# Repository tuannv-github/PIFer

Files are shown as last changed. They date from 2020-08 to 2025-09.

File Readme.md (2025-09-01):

# PIFWRobot

<p align="center">
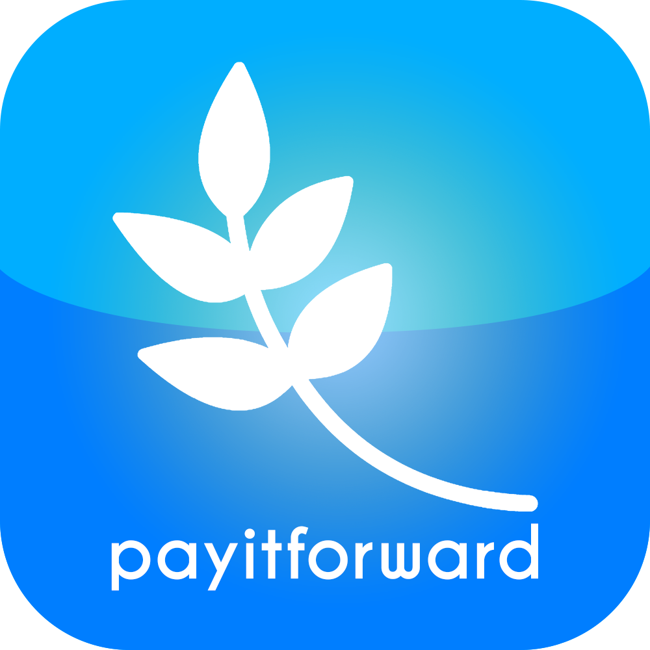
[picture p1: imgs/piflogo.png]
PIF Logo
  
</p>

PIFWRobot is an open source project for a two-wheeled self-balancing robot.

## Demo

Youtube:
* https://www.youtube.com/watch?v=qJoEQ5KJzxM&t=71s&pp=ygUjdHdvIHdoZWVsIHNlbGYgYmFsYW5jaW5nIHJvYm90IHR1YW4%3D
* https://www.youtube.com/watch?v=bJMFOIG7K60&t=61s

Without any velocity command, the robot is trying to stabilize itself. 
<p align="center">
  PIF Logo
</p>

## Repository Contents
* **firmware**: 
  * **balancing-robot**: The entire firmware for STM32F103C8T6 MCU
  * **esp8266_arduino**: ESP8266 Arduino based TCP server firmware
* **software**:
  * **GCSQt**: A Qt-based ground control station for remote controlling, calibration, and PID tuning
  * **mavlink**: Mavlink message definitions and code generation tools
* **hardware**:
  * **board**: Altium-designed schematic and PCB source for the main board
  * **frame**: SolidWorks-based frame source for the robot

## Hardware
*  1 STM32F103C8T6
*  1 MPU6050/9250
*  2 DC Motors with Encoder
*  1 ESP8266 for remote control, calibration, and PID tuning
*  1 L298 DC Motor Driver
*  1 12V Li-po battery 

## PID algorithm
Cascade PID:
* Inner loop: tilt controller
  * Input: 
    * Tilt set point from outer loop
    * Feed back tilt from sensor (MPU6050/9250)
  * Output:
    * PWM duty cycle for both motors
* Outer loop: velocity controller
  * Input:
    * Velocity command from rthe emote controller
    * Feed back velocity from encoder
  * Output:
    * Tilt for inner loop

## License & copyright
@ Van Tuan Ngo, Ho Chi Minh City University of Technology

Licensed under the [MIT license](LICENSE)

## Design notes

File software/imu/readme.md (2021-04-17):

```
python3 imu_data_logger.py -p /dev/ttyUSB0 -b 57600 -o calib_gyro
```

```
python3 imu_data_logger.py -p /dev/ttyUSB0 -b 57600 -o calib_mag
```

```
python3 imu_data_logger.py -p /dev/ttyUSB0 -b 57600 -o imu_data
```

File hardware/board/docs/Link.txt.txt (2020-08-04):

https://www.rohm.com/electronics-basics/dc-dc-converters/linear-vs-switching-regulators

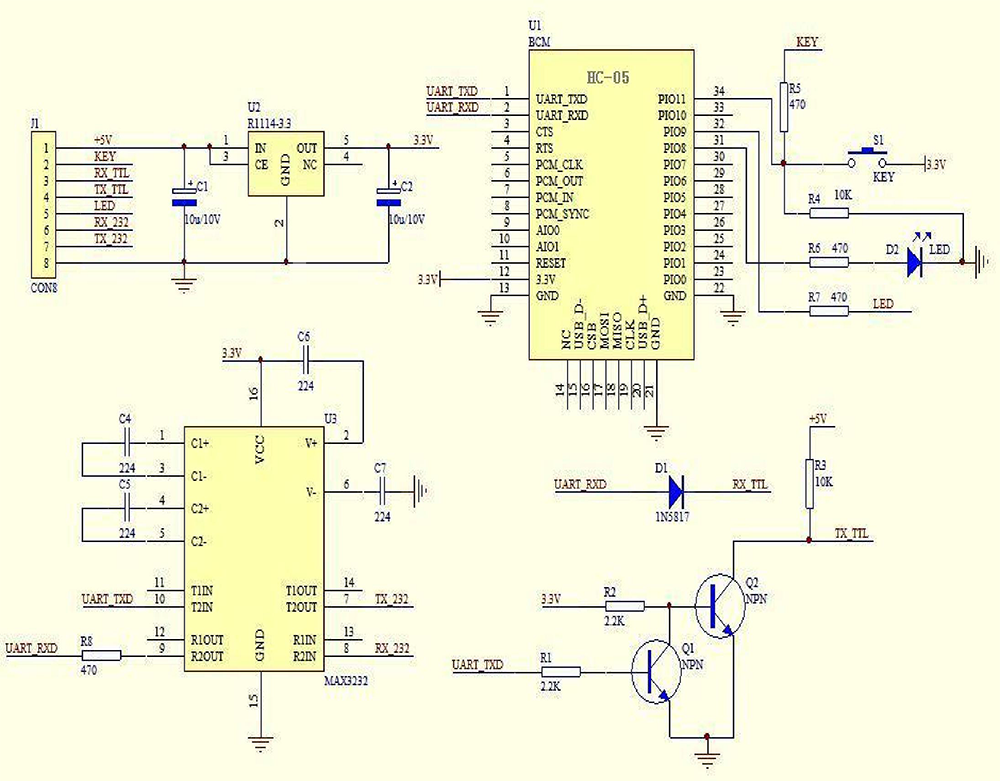
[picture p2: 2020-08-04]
hardware/board/docs/HC-05_schematic_02.png

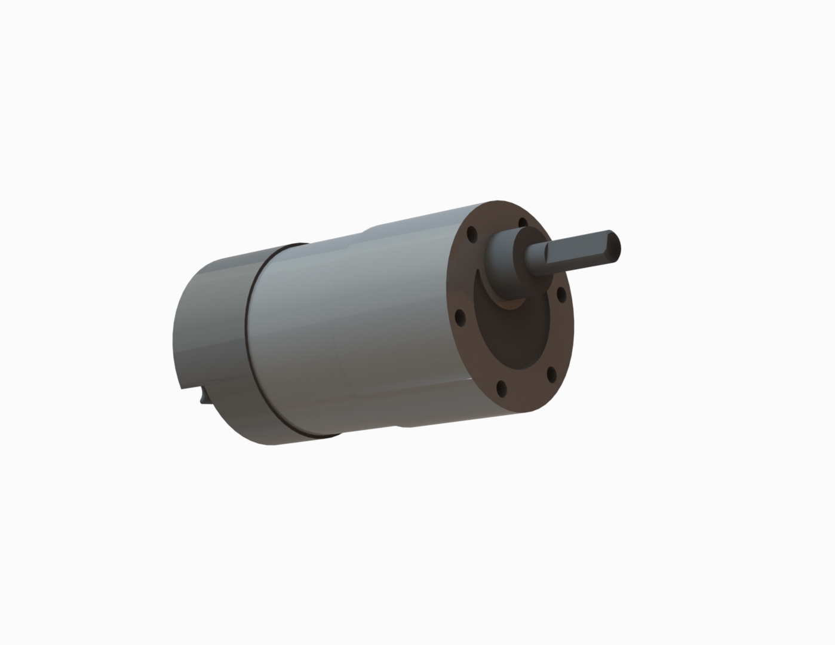
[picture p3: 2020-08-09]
hardware/frame/DCMotor/cytron.jpg

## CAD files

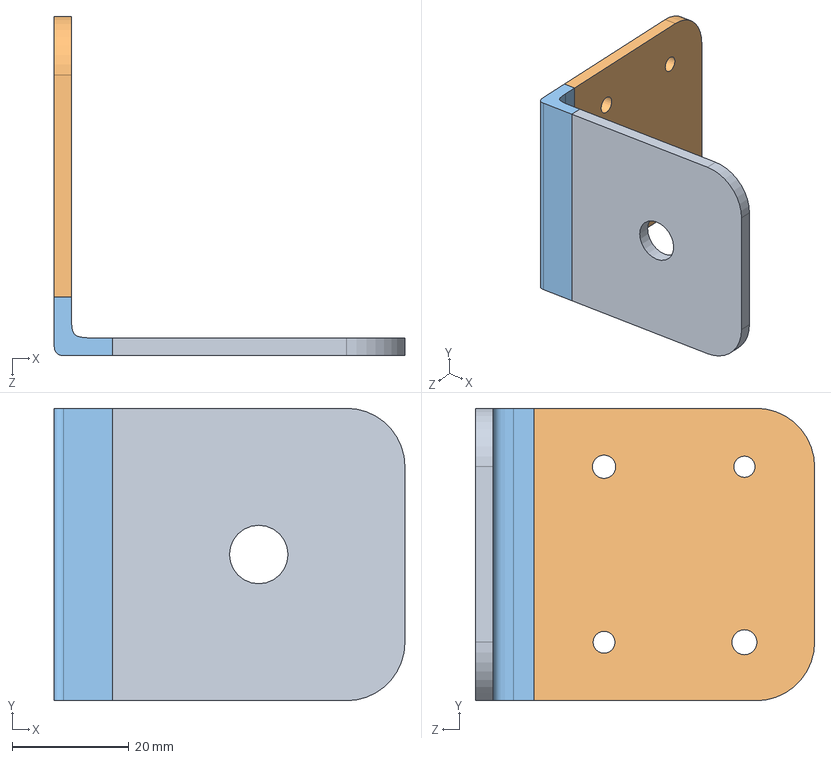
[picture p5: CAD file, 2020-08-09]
hardware/frame/Motor Frame/Assem2.SLDASM
60.0 x 50.0 x 58.0 mm

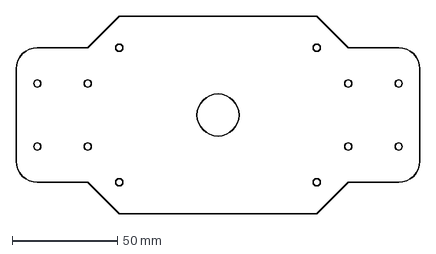
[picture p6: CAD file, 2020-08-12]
hardware/frame/Corel/Part1.DXF
192.0 x 94.0 mm

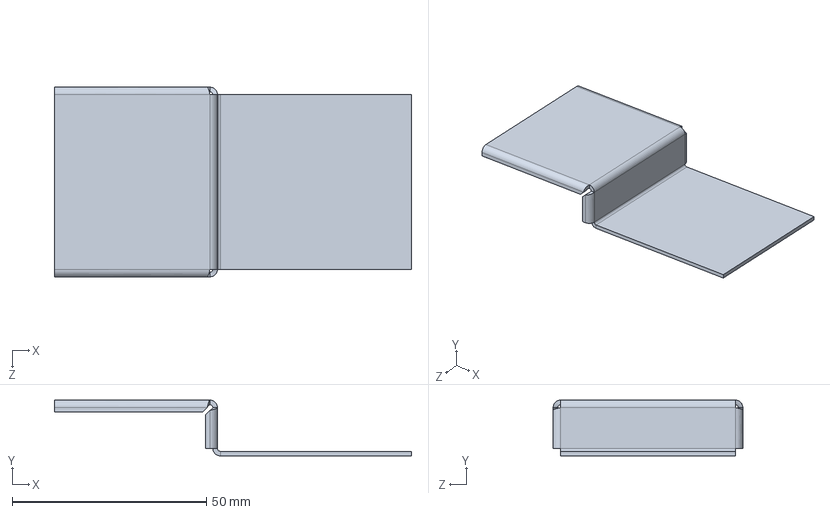
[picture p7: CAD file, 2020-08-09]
hardware/frame/DCMotor/Cytron Motor Plate.SLDPRT
92.0 x 14.4 x 48.9 mm

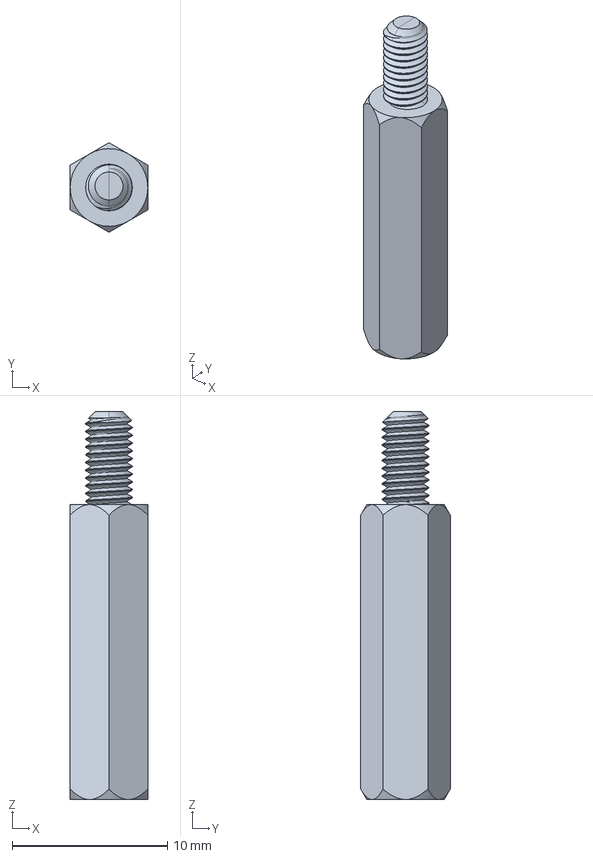
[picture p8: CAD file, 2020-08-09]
hardware/frame/M3/Hex Spacer MF M3 L19mm.stp
5.00 x 5.77 x 25.0 mm

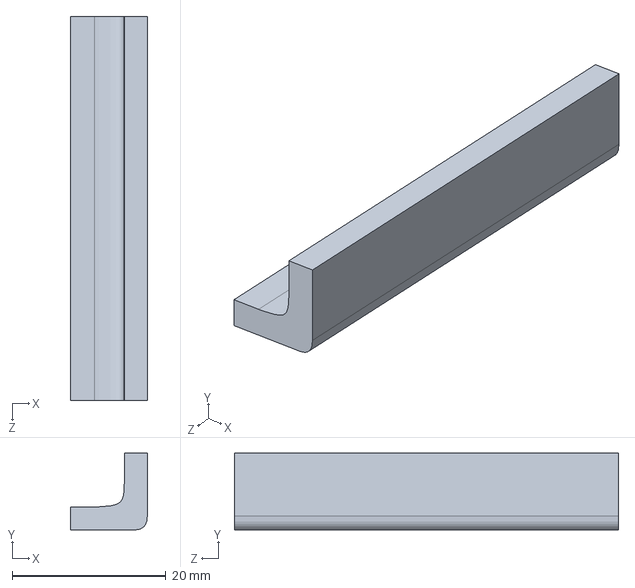
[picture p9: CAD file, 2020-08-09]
hardware/frame/Motor Frame/Part6.SLDPRT
10.0 x 10.0 x 50.0 mm

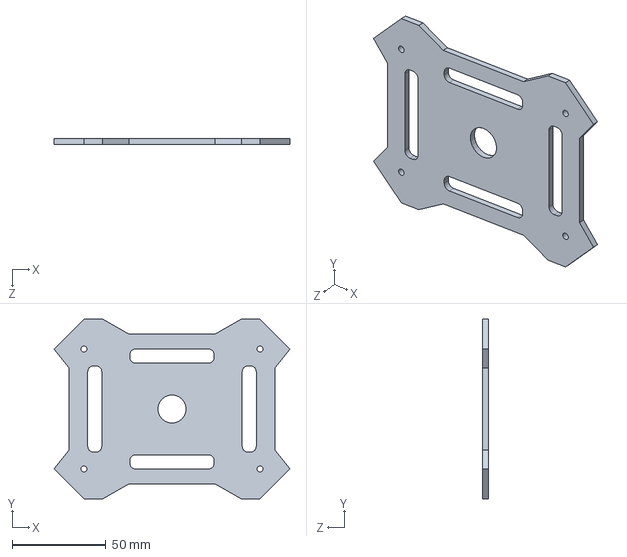
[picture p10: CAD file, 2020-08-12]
hardware/frame/Part3.SLDPRT
126.0 x 96.0 x 3.00 mm

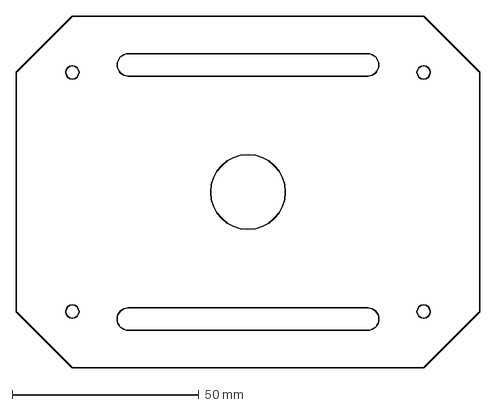
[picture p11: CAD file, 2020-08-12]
hardware/frame/Corel/Part2.DXF
124.0 x 94.0 mm

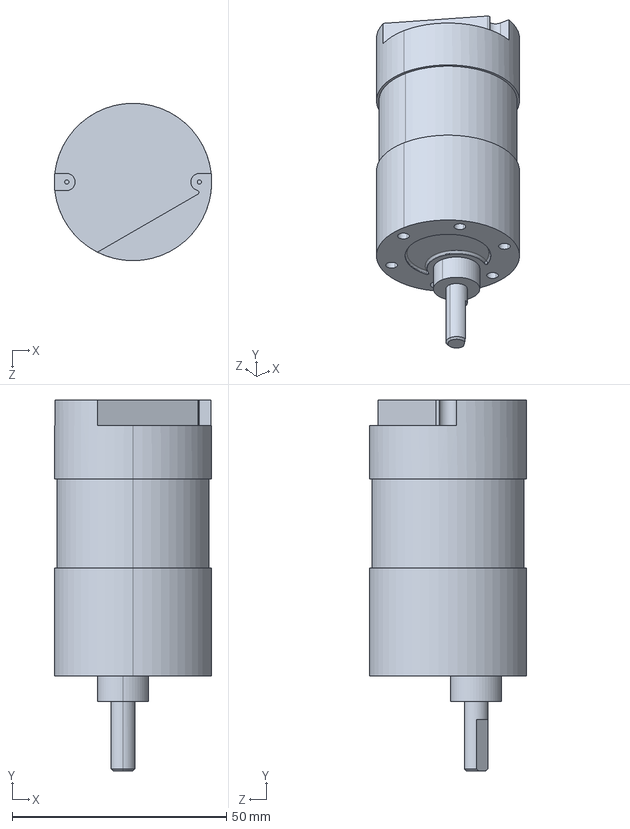
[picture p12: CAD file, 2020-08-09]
hardware/frame/DCMotor/Cytron Motor.STEP
36.7 x 86.5 x 36.7 mm

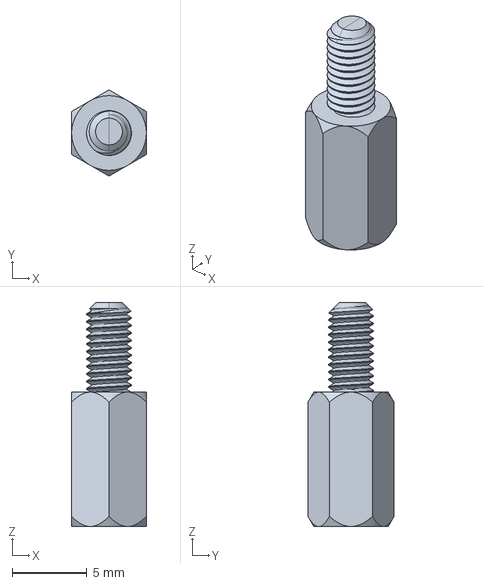
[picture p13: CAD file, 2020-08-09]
hardware/frame/M3/Hex Spacer MF M3 L9mm.stp
5.00 x 5.77 x 15.0 mm

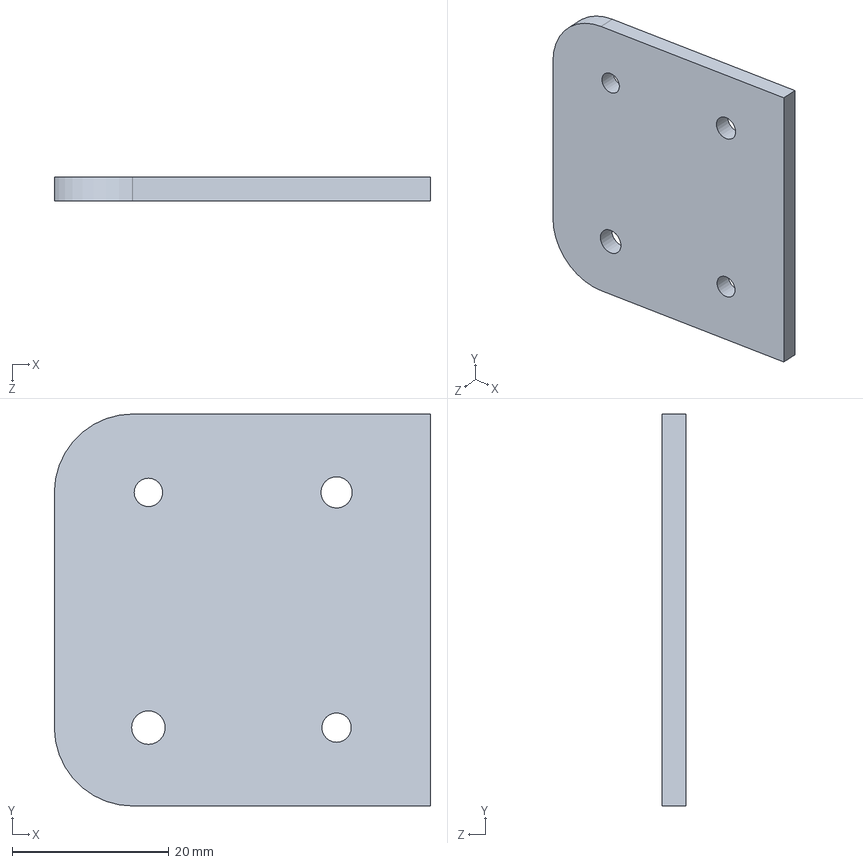
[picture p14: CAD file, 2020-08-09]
hardware/frame/Motor Frame/Part4.SLDPRT
48.0 x 50.0 x 3.00 mm

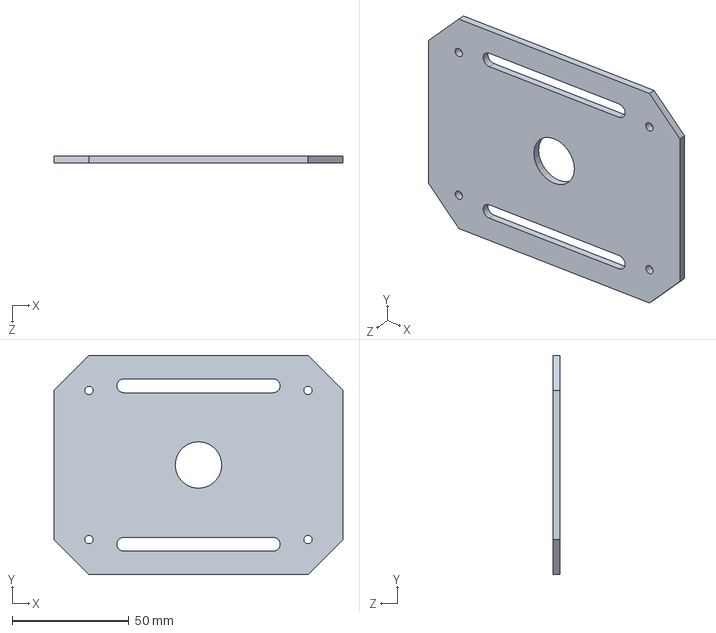
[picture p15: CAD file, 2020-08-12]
hardware/frame/Part2.SLDPRT
124.0 x 94.0 x 3.00 mm

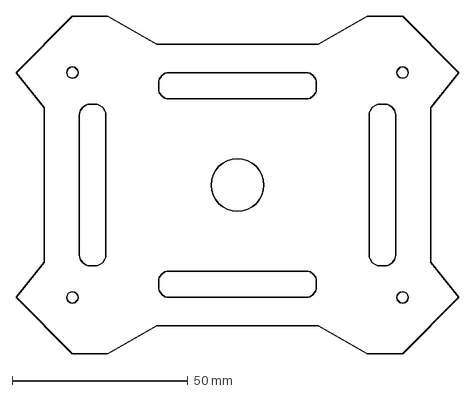
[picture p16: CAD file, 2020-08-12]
hardware/frame/Corel/Part3.DXF
126.0 x 96.0 mm

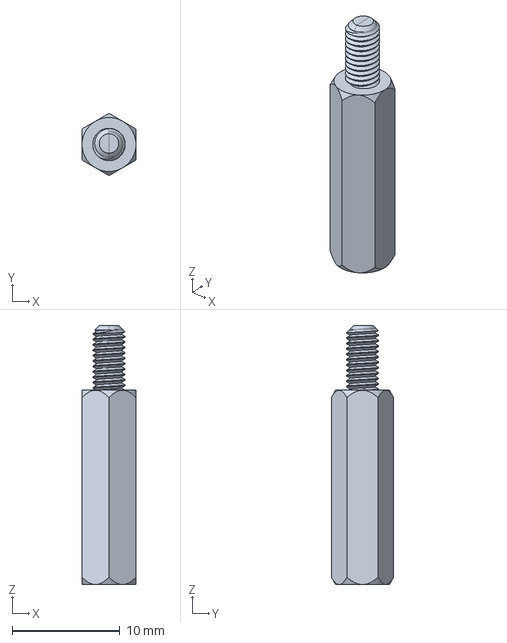
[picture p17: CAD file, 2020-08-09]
hardware/frame/M3/Hex Spacer MF M3 L18mm.stp
5.00 x 5.77 x 24.0 mm

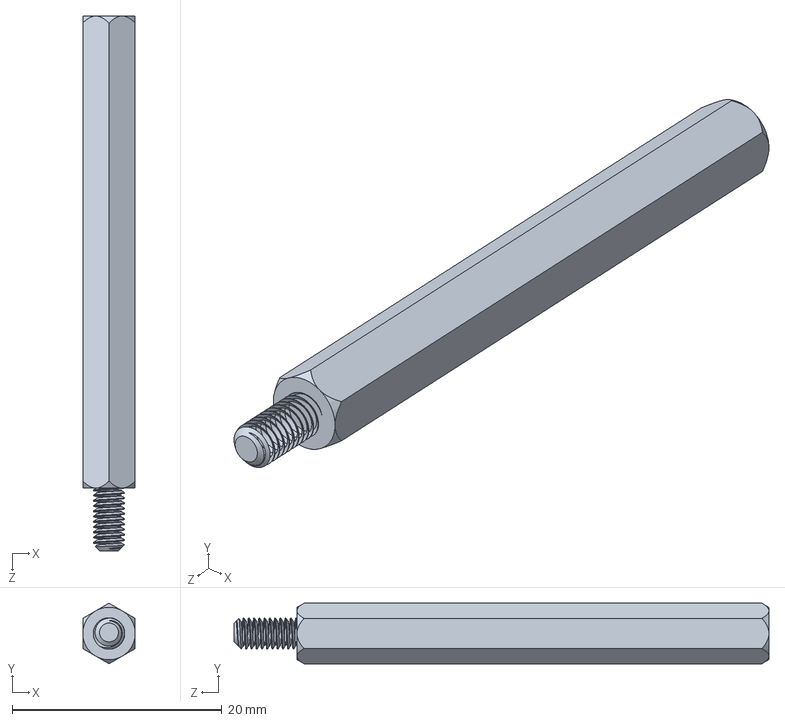
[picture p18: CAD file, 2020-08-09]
hardware/frame/MFM3L45mm.SLDPRT
5.00 x 5.77 x 51.0 mm

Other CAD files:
hardware/frame/Motor Frame/Part5.SLDPRT
hardware/frame/Hex Spacer MF M3 L10mm.SLDPRT
hardware/frame/M3/Hex Spacer MF M3 L40mm.stp
hardware/frame/M3/Hex Spacer MF M3 L12mm.stp
hardware/frame/Axle.SLDPRT
hardware/frame/DCMotor/Cytron Motor.SLDPRT
hardware/frame/FFM3L45mm.SLDPRT
hardware/frame/M3 Nut.SLDPRT
hardware/frame/M3/Hex Spacer MF M3 L10mm.stp
hardware/frame/M3/Hex Spacer MF M3 L11mm.stp
hardware/frame/M3/Hex Spacer MF M3 L13mm.stp
hardware/frame/M3/Hex Spacer MF M3 L14mm.stp
hardware/frame/M3/Hex Spacer MF M3 L15mm.stp
hardware/frame/M3/Hex Spacer MF M3 L16mm.stp
hardware/frame/M3/Hex Spacer MF M3 L17mm.stp
hardware/frame/M3/Hex Spacer MF M3 L20mm.stp
hardware/frame/M3/Hex Spacer MF M3 L25mm.stp
hardware/frame/M3/Hex Spacer MF M3 L30mm.stp
hardware/frame/M3/Hex Spacer MF M3 L35mm.stp
hardware/frame/M3/Hex Spacer MF M3 L45mm.stp
hardware/frame/M3/Hex Spacer MF M3 L50mm.stp
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

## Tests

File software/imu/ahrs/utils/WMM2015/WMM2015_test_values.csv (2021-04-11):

Date | Height(km) | Lat (deg) | (deg) Lon | X (nT) | Y (nT) | Z (nT) | H (nT) | F (nT) | I (deg) | D (deg) | GV (deg) | (nT/yr) Xdot | (nT/yr) Ydot | (nT/yr) Zdot | (nT/yr) Hdot | (nT/yr) Fdot | (deg Idot /yr) | (deg Ddot /yr)
2015 | 0 | 80 | 0 | 6627.1 | -445.9 | 54432.3 | 6642.1 | 54836 | 83.04 | -3.85 | -3.85 | -11.1 | 51.5 | 10.8 | -14.5 | 8.9 | 0.02 | 0.44
2015 | 0 | 0 | 120 | 39518.2 | 392.9 | -11252.4 | 39520.2 | 41090.9 | -15.89 | 0.57 | 0.57 | 21.3 | -68.2 | 88.9 | 20.6 | -4.5 | 0.13 | -0.1
2015 | 0 | -80 | 240 | 5797.3 | 15761.1 | -52919.1 | 16793.5 | 55519.8 | -72.39 | 69.81 | 309.81 | 30.6 | 8.1 | 92.4 | 18.2 | -82.6 | 0.05 | -0.09
2015 | 100 | 80 | 0 | 6314.3 | -471.6 | 52269.8 | 6331.9 | 52652 | 83.09 | -4.27 | -4.27 | -9.5 | 49.2 | 9.1 | -13.2 | 7.5 | 0.02 | 0.44
2015 | 100 | 0 | 120 | 37535.6 | 364.4 | -10773.4 | 37537.3 | 39052.7 | -16.01 | 0.56 | 0.56 | 20 | -61.9 | 83.7 | 19.4 | -4.4 | 0.13 | -0.09
2015 | 100 | -80 | 240 | 5613.1 | 14791.5 | -50378.6 | 15820.7 | 52804.4 | -72.57 | 69.22 | 309.22 | 28.2 | 6.9 | 86.2 | 16.5 | -77.3 | 0.05 | -0.09
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

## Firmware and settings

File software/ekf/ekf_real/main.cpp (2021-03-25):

#include <iostream>
#include <fstream>
#include <string>
#include <vector>
#include <sstream>

#include "ekf.h"
#include "utils.h"

using namespace std;

#define pule_per_revolution     780
#define wheel_diameter          0.065

ekf_t ekf;
ekf_params_t ekf_params = {
    .robot_width = 0.24,
    .control_motion_factor = 0.001f,
    .control_turn_factor = 0.001f,

    .tag_cart_x = 0.0f,
    .tag_cart_y = 0.0f,

    .measurement_distance_stddev = 0.05f,
    .measurement_angle_stddev = 10.0 / 180.0 * M_PI,
};

int main(){
    string line;
    ifstream file_control_measurement("../control_measurement.txt");
    ofstream file_correction("../correction.txt");

    sphere_t spheres[3];
    uint8_t sphere_idx = 0;
    float yaw = 0;
    while (getline(file_control_measurement, line))
    {
        vector<string> components = split(line, " ");
        if(components[0] == "M"){
            cout << line << endl;
            spheres[sphere_idx].x = stof(components[1]);
            spheres[sphere_idx].y = stof(components[2]);
            spheres[sphere_idx].z = 3;
            spheres[sphere_idx].r = stof(components[4]);
            yaw = stof(components[5])/180*M_PI;
            sphere_idx++;
            if(sphere_idx == 3) break;
        }
    }

    trilateration_result_t trilateration_result;
    trilaterate(spheres, &trilateration_result);
    cout << trilateration_result.PA.x << " "
    << trilateration_result.PA.y << " "
    << trilateration_result.PA.z << " "
    << yaw << "\n";

    ekf.x = trilateration_result.PA.x;
    ekf.y = trilateration_result.PA.y;
    ekf.theta = yaw;

    ekf.cov[0][0] = 0.1;
    ekf.cov[1][1] = 0.1;
    ekf.cov[2][2] = (50.0 / 180.0 * M_PI);
    
    ekf.cov[0][0] = ekf.cov[0][0]*ekf.cov[0][0];
    ekf.cov[1][1] = ekf.cov[1][1]*ekf.cov[1][1];
    ekf.cov[2][2] = ekf.cov[2][2]*ekf.cov[2][2];

    ekf_init(&ekf, &ekf_params);
    
    int cnt = 0;
    while (getline(file_control_measurement, line))
    {
        vector<string> components = split(line, " ");
        if(components[0] == "C"){
            float l = -stof(components[1]);
            float r = -stof(components[2]);
            ekf_control_t control;
            control.l = l/pule_per_revolution*(M_PI*wheel_diameter);
            control.r = r/pule_per_revolution*(M_PI*wheel_diameter);
            ekf_predict(&ekf, &control);
        }
        else if(components[0] == "M"){
            ekf_measurement_t m;
            m.rx = stof(components[1]);
            m.ry = stof(components[2]);
            if (fabs(m.rx) < 1 && fabs(m.ry) < 1) continue;
            m.range = sqrt(stof(components[4])*stof(components[4]) - 3*3);
            m.yaw = stof(components[5])/180*M_PI;
            // printf("m: %f %f %f %f\n", m.rx, m.ry, m.range, m.yaw);
            ekf_correct(&ekf, &m);
            file_correction << "F " << ekf.x*300+500 << " " << ekf.y*300+3000 << " " << ekf.theta << endl;
            // cnt++;
            // if(cnt == 10) break;
        }
    }

    // for(int i=0; i<controls.size(); i++){
    //     cout << i << endl;
        // ekf_predict(&ekf_fake, &controls[i]);
        // file_prediction << "F " << ekf_fake.x << " " << ekf_fake.y << " " << ekf_fake.theta << endl;
        // file_prediction << "E " << ekf_fake.cov[0][0] << " " \
        //                         << ekf_fake.cov[0][1] << " " \
        //                         << ekf_fake.cov[0][2] << " " \
        //                         << ekf_fake.cov[1][0] << " " \
        //                         << ekf_fake.cov[1][1] << " " \
        //                         << ekf_fake.cov[1][2] << " " \
        //                         << ekf_fake.cov[2][0] << " " \
        //                         << ekf_fake.cov[2][1] << " " \
        //                         << ekf_fake.cov[2][2] << endl;

    //     cout << "C: " << controls[i].r << " " <<controls[i].l << endl;
    //     ekf_predict(&ekf, &controls[i]);
    //     cout << ekf.x << " " << ekf.y << " " << ekf.theta << endl;
    //     for(int j=0; j<measurements[i].size(); j++){
    //         ekf_correct(&ekf, &measurements[i][j]);
    //         cout << "M: " << measurements[i][j].rx << " " << measurements[i][j].ry << " " << measurements[i][j].range << " " << measurements[i][j].yaw << endl;
    //         cout << ekf.x << " " << ekf.y << " " << ekf.theta << endl;
    //     }
    //     cout << "---------" << endl;

    //     file_correction << "F " << ekf.x << " " << ekf.y << " " << ekf.theta << endl;
    //     file_correction << "E " << ekf.cov[0][0] << " " \
    //                             << ekf.cov[0][1] << " " \
    //                             << ekf.cov[0][2] << " " \
    //                             << ekf.cov[1][0] << " " \
    //                             << ekf.cov[1][1] << " " \
    //                             << ekf.cov[1][2] << " " \
    //                             << ekf.cov[2][0] << " " \
    //                             << ekf.cov[2][1] << " " \
    //                             << ekf.cov[2][2] << endl;

    //     // if(i==686) break;
    // }

    file_control_measurement.close();
    file_correction.close();
    return 0;
}

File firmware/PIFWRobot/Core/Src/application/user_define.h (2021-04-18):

/*
 * user_define.h
 *
 *  Created on: Oct 9, 2019
 *      Author: 16138
 */

#ifndef _USERCODE_USER_DEFINE_H_
#define _USERCODE_USER_DEFINE_H_

#include "main.h"
#include "dma.h"
#include "i2c.h"
#include "spi.h"
#include "tim.h"
#include "usart.h"
#include "gpio.h"

// Self-balancing-DC	--> 0
// Turtle-Step			--> 1
#define ROBOT_MODEL		1

// Enable				--> 1
// Disable				--> 0
#define ENABLE_NEOPIXEL	0

// Timer callback define
#define MAX_CALLBACK_FUNC	15

/* IMU definition */
#define MPU9250_I2C			hi2c1
#define MPU9250_I2C_ADDR	(0x68 << 1)
#define AK8963_I2C_ADDR		(0x0c << 1)
#define I2C_TIMEOUT_MS		20

//GFS_SEL_250DPS	--> 0
//GFS_SEL_500DPS	--> 1
//GFS_SEL_1000DPS	--> 2
//GFS_SEL_2000DPS	--> 3
#define GFS_SEL			0

//AFS_SEL_2G		--> 0
//AFS_SEL_4G		--> 1
//AFS_SEL_8G		--> 2
//AFS_SEL_16G		--> 3
#define ACCEL_FS_SEL	0
/* End of IMU definition */

// DC				--> 0
// STEP				--> 1
#if ROBOT_MODEL==0
#define MOTOR_TYPE		0
#elif ROBOT_MODEL==1
#define MOTOR_TYPE		1
#endif

// Motor 0 define
#if MOTOR_TYPE == 0
	#define MOTOR0_TIMER 		htim2
	#define MOTOR0_CHANNEL 		TIM_CHANNEL_1
	#define MOTOR0_ENCODER		htim3
#elif MOTOR_TYPE==1
	#define MOTOR0_TIMER		htim3
	#define MOTOR0_CHANNEL		TIM_CHANNEL_1
	#define MOTOR0_DIR_PORT		GPIOC
	#define MOTOR0_DIR_PIN		GPIO_PIN_14
#endif

// Motor 1 define
#if MOTOR_TYPE == 0
	#define MOTOR1_TIMER 		htim2
	#define MOTOR1_CHANNEL 		TIM_CHANNEL_2
	#define MOTOR1_ENCODER		htim4
#elif MOTOR_TYPE==1
	#define MOTOR1_TIMER		htim4
	#define MOTOR1_CHANNEL  	TIM_CHANNEL_2
	#define MOTOR1_DIR_PORT		GPIOD
	#define MOTOR1_DIR_PIN		GPIO_PIN_0
#endif

// Motor common define
#define ENC_PERIOD		100
#define ENC_RP_PERIOD	(2*ENC_PERIOD)

// IMU define
#define MPU6050_I2C			hi2c1
#define MPU9250_I2C			hi2c1
#define MPU6050_ADDRESS 	(MPU6050_DEFAULT_ADDRESS << 1)
#define TILT_PERIOD_MS		2
#define RPY_PERIOD_MS		10
#define IMU_RAW_RP_PERIOD	45
#define IMU_CAL_RP_PERIOD	55
#define IMU_RPY_RP_PERIOD	60

// UART
#define MAX_UART_INSTANT	3
#define TX_DMA_BUF_SIZE 	512
#define RX_DMA_BUF_SIZE		512
#define TX_CIR_BUF_SIZE 	512
#define RX_CIR_BUF_SIZE 	512

// Serial to DWM1001
#define STD_USART			huart1
#define STD_PERIOD			100

// Serial over ESP8266
#define SOE_USART			huart2
#define SOE_PERIOD			100

// Serial over UART define
#define SOU_USART			huart3
#define SOU_PERIOD			100

// Mavlink
#define MAV_BUFF_SIZE 		128
#define MAVLINK_CB_PERIOD	15	// Mavlink read message callback

// Parameters define
#define PARAMS_PAGE_ADDRESS 		0x0800FC00
#define HAVE_SAVED_DATA				0x01

// ROBOT_MODEL_TWO_WHEELS mode RUN
#define TILT_CONTROLLER_PERIOD		5
#define VEL_CONTROLLER_PERIOD		100
#define IMU_STATUS_REPORT_PERIOD	100
#define RPY_REPORT_PERIOD			100
#define MODE_RUN_REPORT_PERIOD		100
#define CONTROL_TIMEOUT_MS			1000
#define VX_TO_TILT					0.04f
#define OMEGA_COEFF					150.0f
#define VELOC_COEFF					250.0f
#define TILT_REPORT_PERIOD			100

// ROBOT_MODEL_TANK general define
#define WHEEL_PERIOD				50
#define SYNC_PERIOD					100

// ROBOT_MODEL_TANK	mode PIDT
#define PID_REPORT_PERIOD			100
#define SPEED_REPORT_PERIOD			100

#define CONST_G 					9.807f

// STEP MOTOR DEFINE
#define PULSES_PER_METER 	8027
#define ROBOT_WIDTH 		0.16f

#endif /* USERCODE_USER_DEFINE_H_ */

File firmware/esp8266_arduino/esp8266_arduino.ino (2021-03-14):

#include <ESP8266WiFi.h>

const char *ssid = "PIFer"; 
const char *password = "payitforward"; 

IPAddress local_IP(192,168,4,1);
IPAddress gateway(192,168,4,1);
IPAddress subnet(255,255,255,0);

int port = 8888;  //Port number
WiFiServer server(port);

int cnt = 0;

void setup()
{
  pinMode(LED_BUILTIN, OUTPUT);
  digitalWrite(LED_BUILTIN, HIGH);
  
  Serial.begin(115200);
  Serial.println();

  WiFi.mode(WIFI_AP);
  WiFi.softAPConfig(local_IP, gateway, subnet);
  WiFi.softAP(ssid, password);
  server.begin();
}

void loop() {
  WiFiClient client = server.available();
  if (client) {
    while(client.connected()){      
      while(client.available()>0){
        // read data from the connected client
        Serial.write(client.read());
        digitalWrite(LED_BUILTIN, LOW);
      }
      while(Serial.available()>0)
      {
        //Send Data to connected client
        client.write(Serial.read());
        digitalWrite(LED_BUILTIN, LOW);
      }
      cnt++;
      if(cnt%500==0) digitalWrite(LED_BUILTIN, HIGH);
    }
    client.stop();
  }
}

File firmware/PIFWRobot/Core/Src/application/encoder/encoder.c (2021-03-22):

/*
 * Encoder.c
 *
 *  Created on: Dec 17, 2019
 *      Author: 16138
 */

#include <application/encoder/encoder.h>
#include <application/params/params.h>
#include <application/timer/timer.h>
#include <application/user_define.h>
#include "tim.h"

#if MOTOR_TYPE==0

typedef int16_t (*enc_read_t)(motors_t motor);
typedef int32_t (*enc_read_acc_t)(motors_t motor);

static int16_t enc_read_0(motors_t motor);
static int16_t enc_read_1(motors_t motor);
static int32_t enc_read_0_acc(motors_t motor);
static int32_t enc_read_1_acc(motors_t motor);

static int16_t 	  		m0_speed=0, m1_speed=0;
static int32_t 	  		m0_speed_acc=0, m1_speed_acc=0;
static enc_read_t 		genc_read = 0;
static enc_read_acc_t 	genc_read_acc = 0;
static timer_id_t 		genc_id;
static bool 			ginitialized = false;

static void enc_callback(void *ctx){
	m0_speed = MOTOR0_ENCODER.Instance->CNT;
	MOTOR0_ENCODER.Instance->CNT = 0;
	m0_speed_acc += m0_speed;

	m1_speed = MOTOR1_ENCODER.Instance->CNT;
	MOTOR1_ENCODER.Instance->CNT = 0;
	m1_speed_acc += m1_speed;
}

int enc_init(){
	if(ginitialized) return 0;

	HAL_TIM_Encoder_Start(&MOTOR0_ENCODER,TIM_CHANNEL_ALL);
	HAL_TIM_Encoder_Start(&MOTOR1_ENCODER,TIM_CHANNEL_ALL);
	MOTOR0_ENCODER.Instance->CNT = 0;
	MOTOR1_ENCODER.Instance->CNT = 0;

	m0_speed_acc = 0;
	m1_speed_acc = 0;

	if(params.encoder_exchange) {
		genc_read = enc_read_0;
		genc_read_acc = enc_read_0_acc;
	}
	else {
		genc_read = enc_read_1;
		genc_read_acc = enc_read_1_acc;
	}

	genc_id = timer_register_callback(enc_callback, ENC_PERIOD, 0, TIMER_MODE_REPEAT);

	ginitialized = true;
	return 0;
}

int enc_deinit(){
	timer_unregister_callback(genc_id);
	ginitialized = false;
	return 0;
}

int16_t enc_read(motors_t motor){
	return genc_read(motor);
}

int32_t enc_read_acc(motors_t motor){
	return genc_read_acc(motor);
}

static int16_t enc_read_0(motors_t motor){
	switch(motor){
	case MOTOR_0:
		if(params.encoder0_invert) return -m0_speed;
		else return m0_speed;
		break;
	case MOTOR_1:
		if(params.encoder1_invert) return -m1_speed;
		else return m1_speed;
		break;
	}
	return 0;
}

static int16_t enc_read_1(motors_t motor){
	switch(motor){
	case MOTOR_0:
		if(params.encoder0_invert) return -m1_speed;
		else return m1_speed;
		break;
	case MOTOR_1:
		if(params.encoder1_invert) return -m0_speed;
		else return m0_speed;
		break;
	}
	return 0;
}

static int32_t enc_read_0_acc(motors_t motor){
	switch(motor){
	case MOTOR_0:
		if(params.encoder0_invert) {
			int32_t tmp = m0_speed_acc;
			m0_speed_acc = 0;
			return -tmp;
		}
		else{
			int32_t tmp = m0_speed_acc;
			m0_speed_acc = 0;
			return tmp;
		}
		break;
	case MOTOR_1:
		if(params.encoder1_invert){
			int32_t tmp = m1_speed_acc;
			m1_speed_acc = 0;
			return -tmp;
		}
		else{
			int32_t tmp = m1_speed_acc;
			m1_speed_acc = 0;
			return tmp;
		}
		break;
	}
	return 0;
}

static int32_t enc_read_1_acc(motors_t motor){
	switch(motor){
	case MOTOR_0:
		if(params.encoder0_invert){
			int32_t tmp = m1_speed_acc;
			m1_speed_acc = 0;
			return -tmp;
		}
		else{
			int32_t tmp = m1_speed_acc;
			m1_speed_acc = 0;
			return tmp;
		}
		break;
	case MOTOR_1:
		if(params.encoder1_invert){
			int32_t tmp = m0_speed_acc;
			m0_speed_acc = 0;
			return -tmp;
		}
		else{
			int32_t tmp = m0_speed_acc;
			m0_speed_acc = 0;
			return tmp;
		}
		break;
	}
	return 0;
}

#endif

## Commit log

2020-05-26 Add LC12S
    [PIFWRobot.PcbLib, PIFWRobot.PrjPcb, PIFWRobot.SchDoc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]
2020-05-26 Add HC12
    [PIFWRobot.PcbLib, PIFWRobot.SchLib]
2020-05-26 Add NRF24L01
    [PIFWRobot.PcbLib, PIFWRobot.PrjPcb, PIFWRobot.SchLib]
2020-05-26 Add Holybro Radio module
    [PIFWRobot.PcbLib, PIFWRobot.SchLib]
2020-05-26 Add HC0506
    [PIFWRobot.PcbLib, PIFWRobot.SchLib]
2020-05-26 Add ESP8266-12E
    Add ESP8266-12E
    [PIFWRobot.PcbLib, PIFWRobot.SchLib]
2020-06-08 Change board design folder
    [PIFWRobot.PrjPcb, PIFWRobot.SchDoc, PIFWRobot.SchLib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]
2020-06-08 remove redundancies
    [PIFWRobot.PcbDoc, PIFWRobot.PcbLib, PIFWRobot.PrjPcb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]
2020-06-08 Schematic has been completed
    [PIFWRobot.PrjPcb, PIFWRobot.SchLib, bluetooth.SchDoc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]
2020-06-10 Fix some bugs
    [bluetooth.SchDoc, decawave.SchDoc, mcu.SchDoc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]
2020-06-17 add docs
    [PIFWRobot.PrjPcb, PIFWRobot.SchLib, bluetooth.SchDoc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]
2020-06-17 Ready for PCB
    [PIFWRobot.PrjPcb, PIFWRobot.SchLib, bluetooth.SchDoc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]
2020-06-20 PCB draft
    [PIFWRobot.PrjPcb, decawave.SchDoc, mcu.SchDoc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]
2020-06-21 new PCB version goes from here
    [mcu.SchDoc, power_supply.SchDoc, sensor.SchDoc]
2020-06-24 PCB need power reroute
    PCB need power reroute
    [PIFWRobot.PrjPcb, motor_controller.SchDoc, sensor.SchDoc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]
2020-06-27 May ready to pcb ordering
    [LogoCLB.PcbLib, LogoCLB.SchLib, PIFWRobot.PrjPcb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]
2020-06-27 PCB ordered
2020-06-29 Order PCB again - Fix 1mil hole bug
    [PIFWRobot.PrjPcb, motor_controller.SchDoc, radio_frequency.SchDoc]
2020-08-04 Update components paramameter
    [LogoCLB.SchLib, PIFWRobot.PrjPcb, PIFWRobot.SchLib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]
2020-08-04 add initial firmware from other project
    [BlancingRobot Run.cfg, BlancingRobot.xml]
2020-08-04 Remove redundant lib
    [PIFWRobot.PrjPcb]
2020-08-04 add frame
    [Assem2.SLDASM, Axle.SLDPRT, Cytron Motor Plate.SLDPRT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]
2020-08-12 Update frame
    [Part1.DXF, Part2.DXF, Part2.SLDPRT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]
2020-08-12 Add esp8266 firmware
    [ESP32_RF_INIT.xlsx, ESP8266_RF_init.xls, ESP8266_RF_init.xlsx]
2020-08-12 update pin config
    [BlancingRobot Run.cfg, BlancingRobot.xml]
2020-08-12 Update firmware for new board
2020-08-15 Fix PCB minor bugs
    [PIFWRobot.PrjPcb]
2020-08-18 Make it more beautiful
    [mcu.SchDoc, power_supply.SchDoc, radio_frequency.SchDoc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]
2020-08-22 Motor and encoder are OK
2020-08-29 see mpu9250 and ak8963
    [BlancingRobot Run.cfg]
2020-08-29 correct template logo and update to project
    [bluetooth.SchDoc, decawave.SchDoc, mcu.SchDoc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]
2020-09-03 IMU mode may be OK
2020-09-05 add motor dead band
2020-09-08 Fix NRF24 CE pin bug
    [mcu.SchDoc, radio_frequency.SchDoc]
2020-09-12 modulate uart driver
2020-09-17 ESP8266 is server
    [ESP32_RF_INIT.xlsx, ESP8266_RF_init.xls, ESP8266_RF_init.xlsx]
2020-09-19 Add D and Out threshold for velocity control
2020-10-09 Android app able to communicate over TCP socket
2021-03-14 move to cubeIDE
    [BlancingRobot Run.cfg, BlancingRobot.xml]
2021-03-14 ignore Debug folder
    [Assem2.SLDASM, Axle.SLDPRT, Cytron Motor Plate.SLDPRT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]
2021-03-18 Enable UART3 to communicate with companion computer
2021-03-20 use +1 UART module
2021-03-20 remove redundant qt slot
2021-03-20 combine gyro accel and mag message
2021-03-21 add imu + madgwick code
2021-03-21 add stepmotor
    [PIFWRobot.PrjPcb]
2021-03-21 step motor --> done
    [PIFWRobot Debug.cfg]
2021-03-21 add madgwick filter
2021-03-21 add complementary filter
2021-03-21 remove redundancy
    [PIFWRobot Debug.cfg]
2021-03-22 add board pdf design file
2021-03-22 update pcb -- topoverlay
2021-03-30 start new board
    [PIFer.PrjPcb, fmu.SchDoc, imu.SchDoc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]
2021-04-04 mode run reports measurement message (distance + yaw)
2021-04-11 update message + add imu data analysis code
    [WMM2015_test_values.csv]
2021-04-17 fix imu read bugs
    [mpu9250.c]
2021-04-18 do not publish imu rpy message
2021-04-18 calib PPS + uplink yaw radian
